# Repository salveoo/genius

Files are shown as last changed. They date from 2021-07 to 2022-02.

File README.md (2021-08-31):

# Artillery Genius to Switchwire
This is my journey in converting an Artillery Genius to Switchwire. \
_discord salveo#6988 if you have any question_

<p align="center">
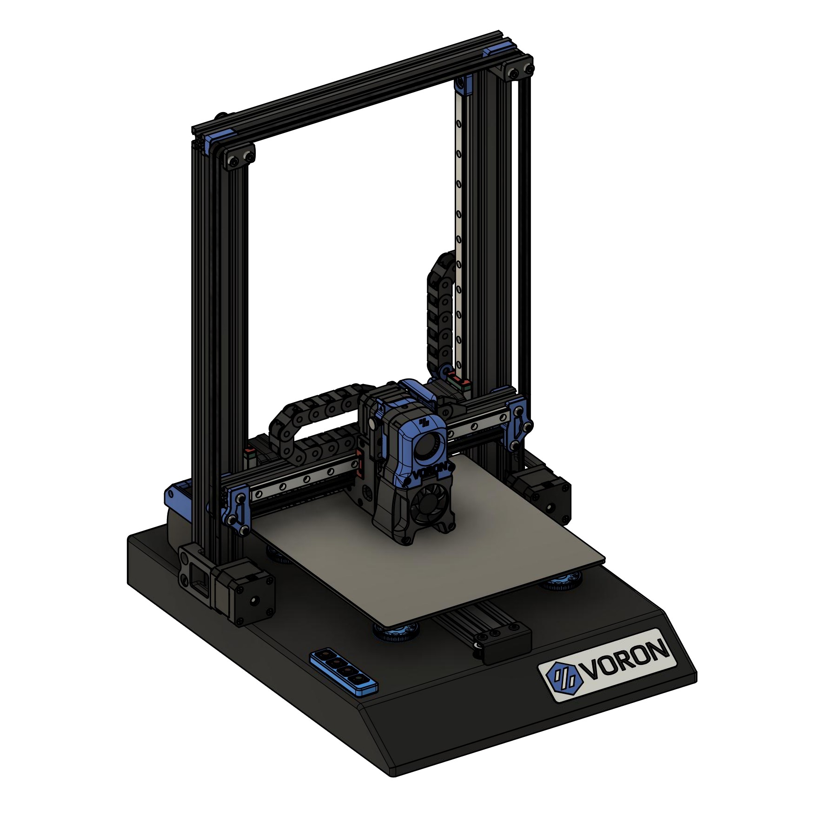
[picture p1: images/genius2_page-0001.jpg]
  
</p>

## SW 193 ♥

<p align="center">
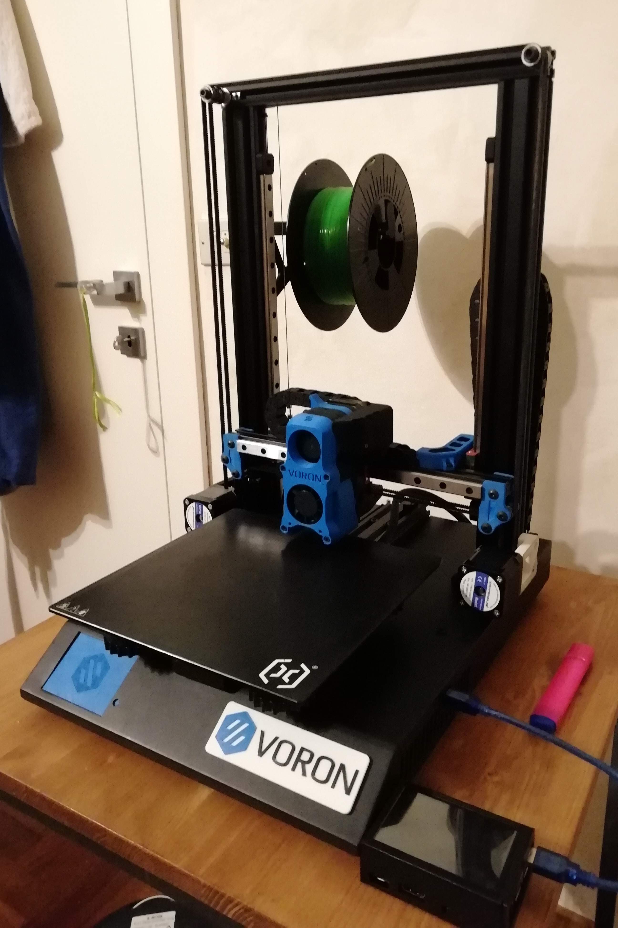
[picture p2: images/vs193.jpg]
  
</p>

## This conversion is based on [Gizzle’s Ender 3 conversion](https://github.com/VoronDesign/VoronUsers/tree/master/printer_mods/Gizzle/ender-3_(pro)_switchwire "Title")

I reused the following parts:
* motor mounts
* upper blocks assembly
* Z bearing blocks
* keybak mount

## Build information
This mod will shorten the X travel by 10mm because of the narrow vertical extrusions but you will gain 20mm of travel in Z. \
**The build volume is 220x230x270** \

## Build overview
_Front and Left_
<p align="center">
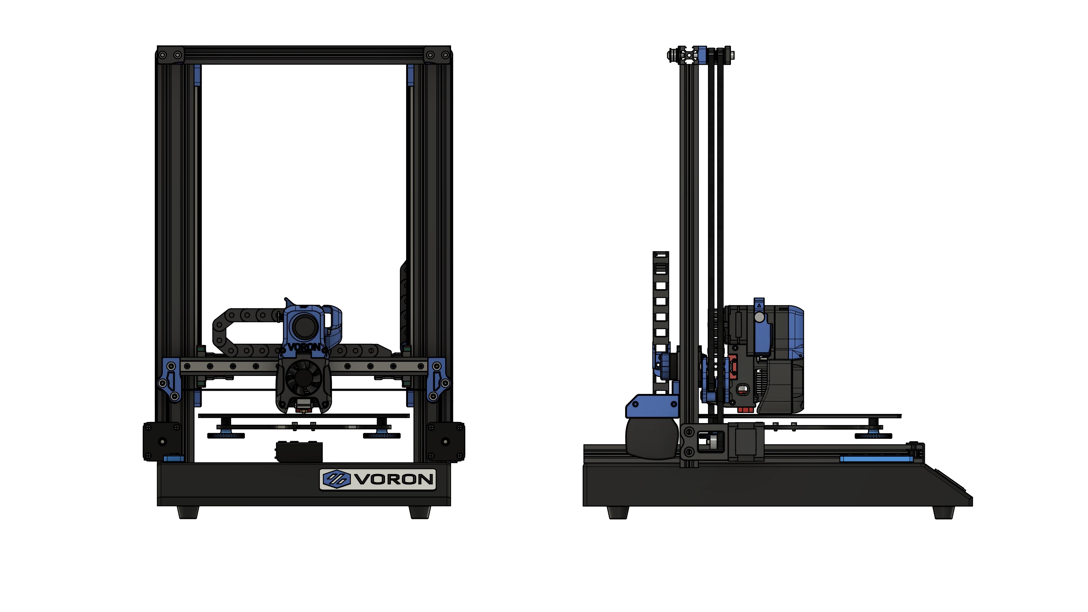
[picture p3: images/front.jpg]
  
</p>

_Back and Right_
<p align="center">
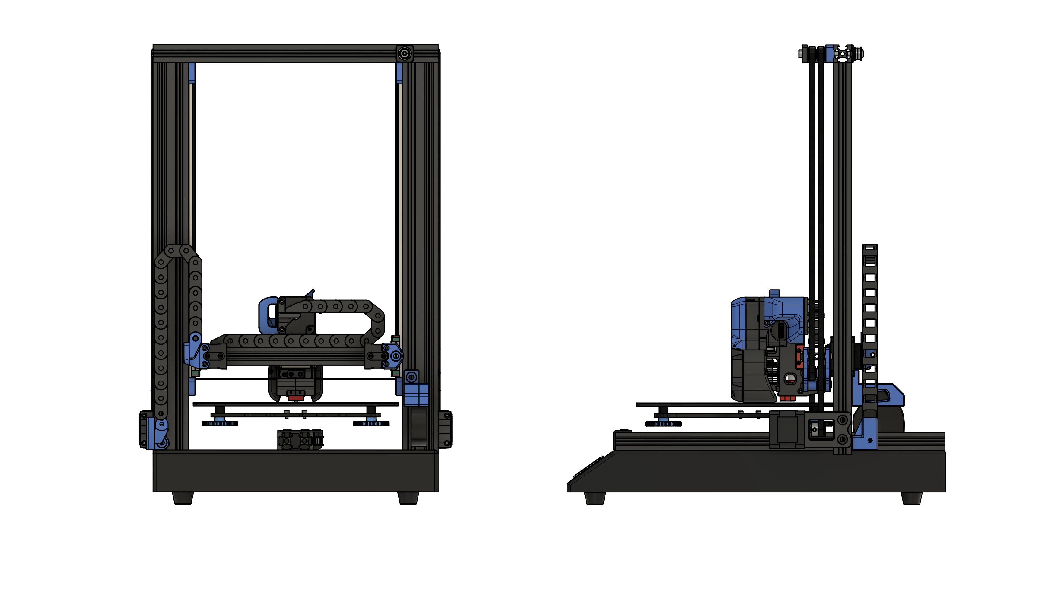
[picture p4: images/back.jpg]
  
</p>

## Reuse parts
You can reuse a good amount of parts from the Genius:
* MCU (Mks gen L)
* PSU
* Y assembly
* All the stepper motors except the extruder one
* 4020 blower
* 4010 fan
* 2040 vertical extrusions \
**At the moment, the TFT screen is not compatible with Klipper, you won’t be able to use it.**

## BOM
[See the Switchwire BOM for links to products](https://vorondesign.com/sourcing_guide?model=VS)

### Frame
* 2020 extrusion 320mm – 1pcs (top extrusion)
* 2020 extrusion 310mm – 1pcs (x axis extrusion)
### Motion
* MGN12H linear rail 330mm – 2pcs (z axis)
* MGN12H linear rail 270mm – 1pcs (x axis)
* GT2 belt – 5 meters
* GT2 20t pulley – 3 pcs
* F695 Bearing – 20 pcs
### Electronics
* Raspberry for running klipper
* SPDT KW10 Limit Micro Switch (for x-axis)
* Omron TL-Q5MC2 - NPN Inductive Probe (if you want bed mesh leveling,I reused the stock endstop for z)
* 20mm NEMA17 for the extruder (NEMA17 Motor 17HS08-1004S)
### Misc
* Loctite Blue Threadlocker (or nail polish)
* Key-Bak (you can use this cheaper alternative (https://it.aliexpress.com/item/1005001273995297.html)

### Cable Management	
* 24 AWG PTFE
* 20 AWG PTFE
* 10x11 Cable Chain
* connectors

### Fasteners
_Make sure you order spare fasteners in case I miscounted them_

<p align="center">
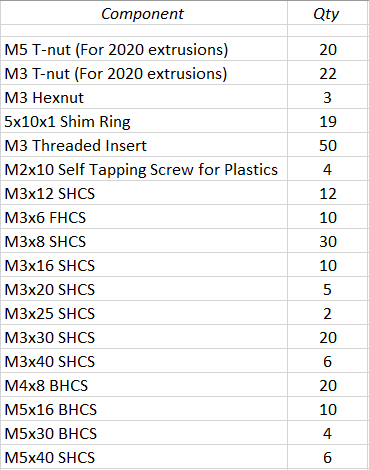
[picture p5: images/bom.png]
  
</p>

### Extra
* hardware for the Afterburner (check sw bom)

## GCODE buttons mod
To cover the unused usb port I created a keyboard of 4 buttons that call a gcode macro. \
Buttons used: 12x12x4.3 => [aliexpress](https://it.aliexpress.com/item/32807507828.html)

<p align="center">
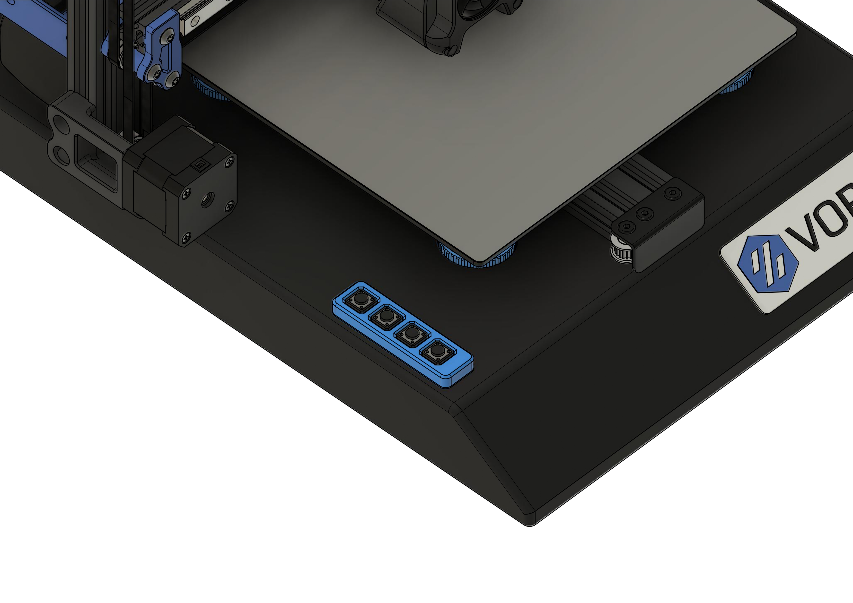
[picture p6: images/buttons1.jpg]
  
</p>

Solder one side of the button to a data pin, the other goes to GND. \
Then close the lid and route the cables through the usb hole.
<p align="center">
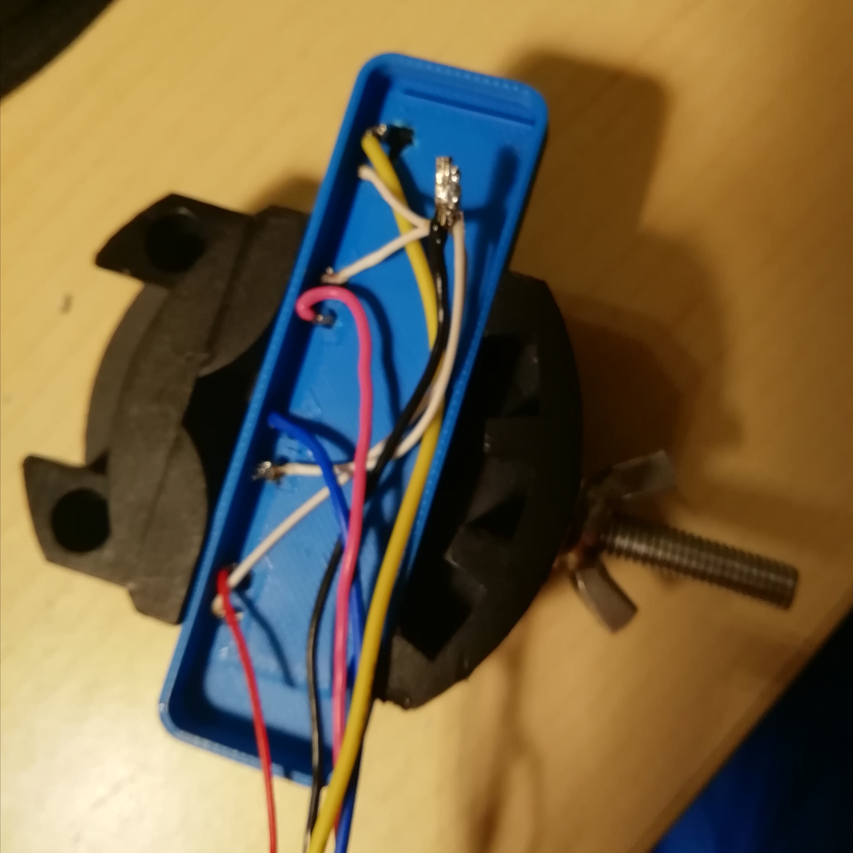
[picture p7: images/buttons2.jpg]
  
</p>

Product in action
<p align="center">
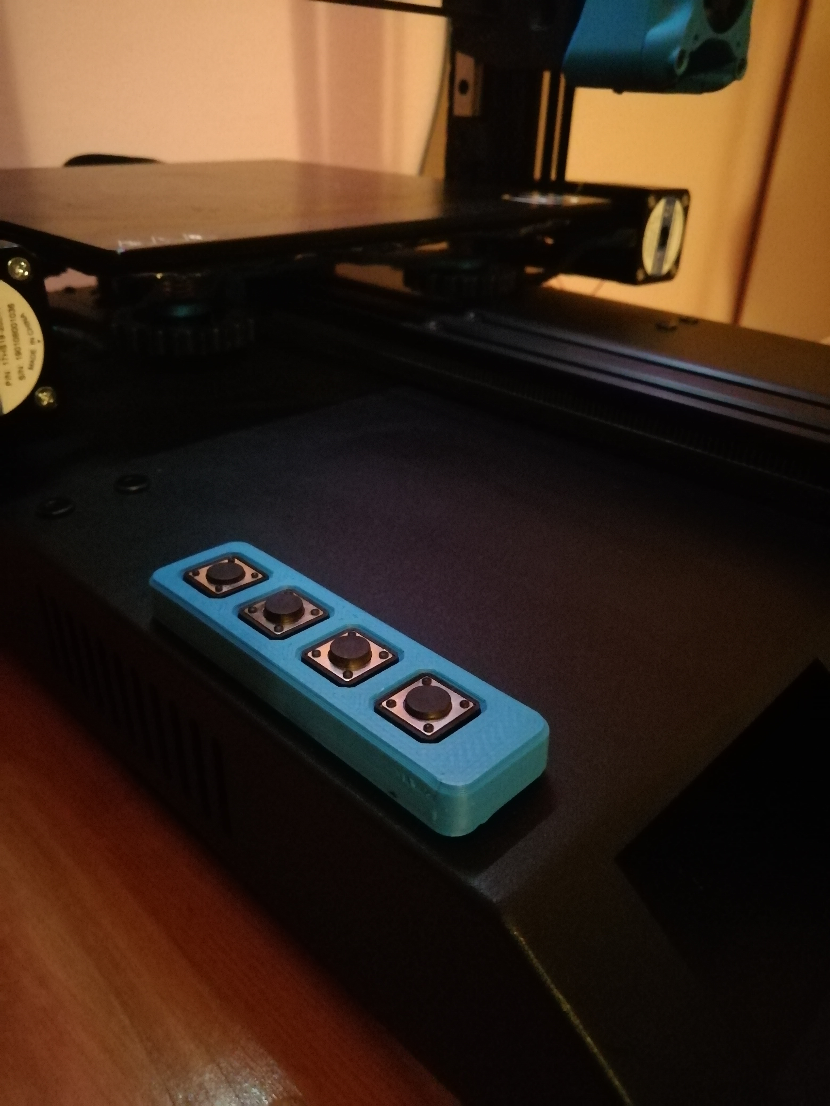
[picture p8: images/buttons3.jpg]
  
</p>

## Full metal idlers
If you want your top idlers to be sturdier you can reuse the old pulley to act as an m5 spacer.
<p align="center">
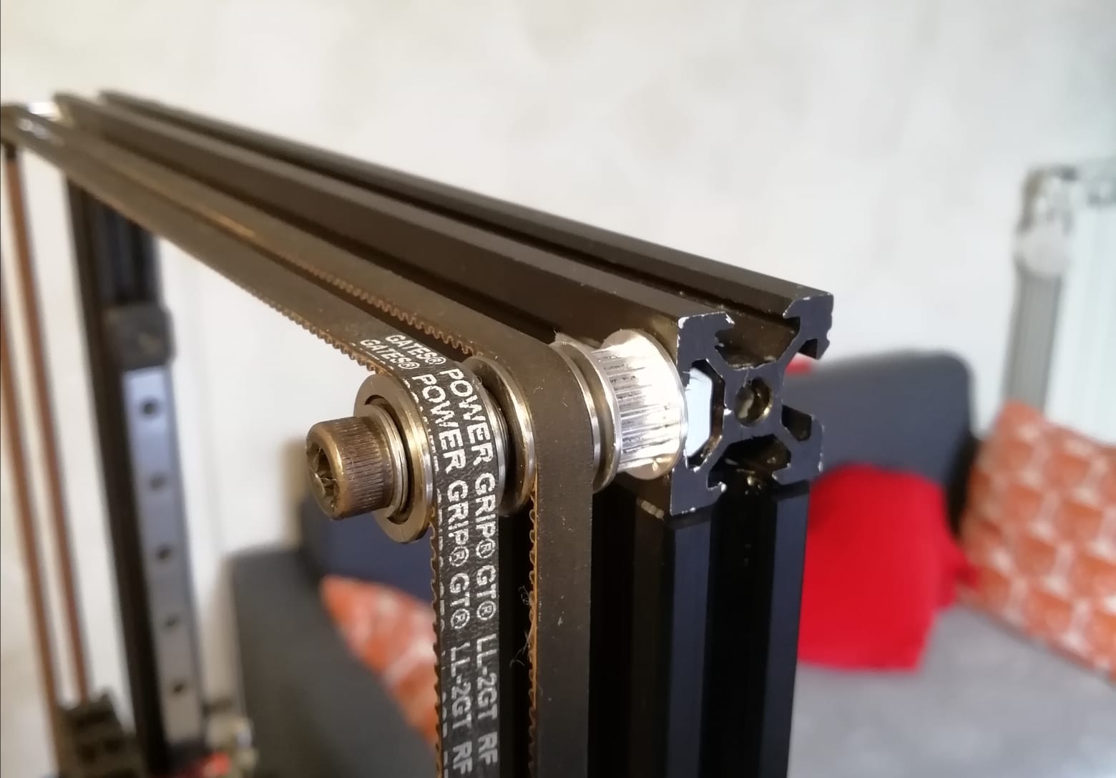
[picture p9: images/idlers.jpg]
  
</p>

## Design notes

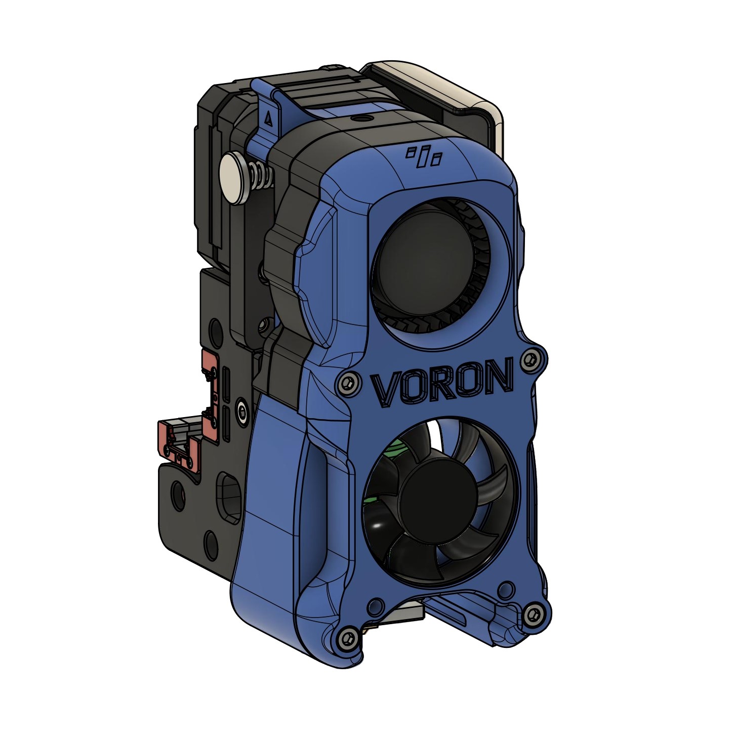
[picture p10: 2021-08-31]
images/mod1.jpg

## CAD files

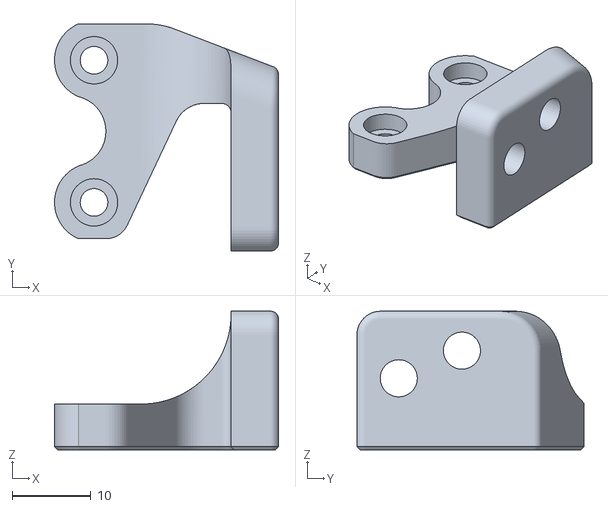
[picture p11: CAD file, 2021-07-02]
STL/CABLE_CHAINS/Z_chain_mount.stl
28.4 x 28.8 x 17.6

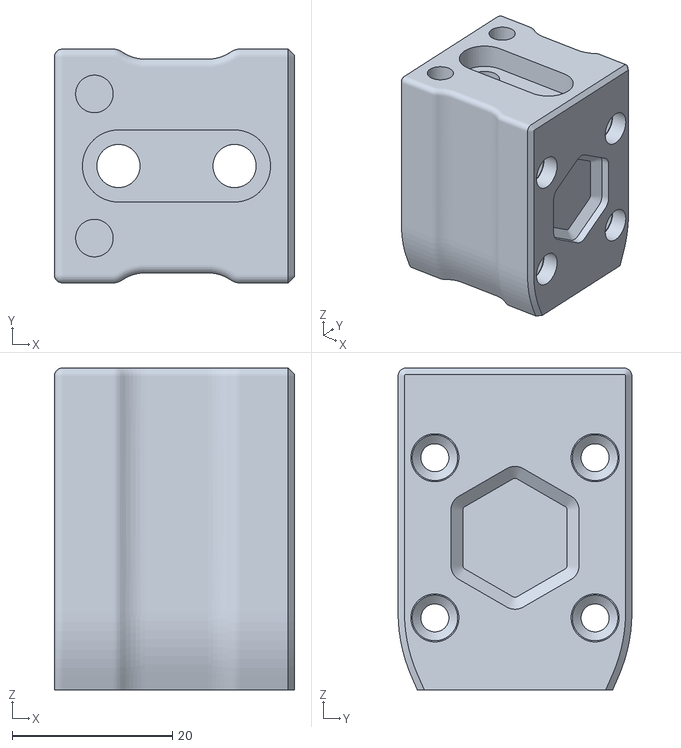
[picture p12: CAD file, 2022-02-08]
STL/GANTRY/Z-Bearing_Block_Right_x1.stl
30.0 x 29.2 x 40.2

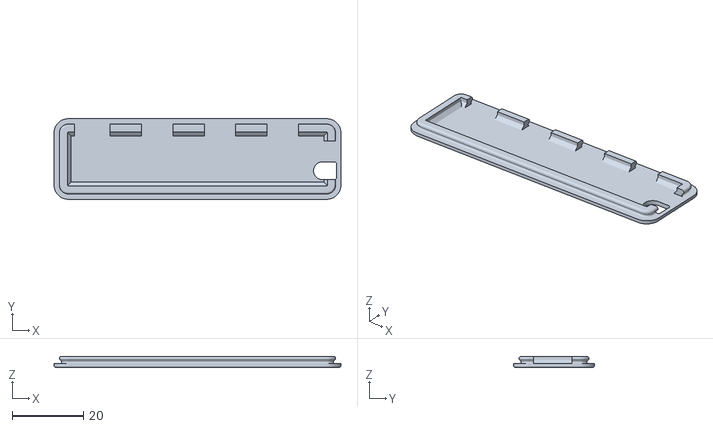
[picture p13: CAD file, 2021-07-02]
STL/GCODE_BUTTONS_MOD/bottom.stl
80.4 x 22.6 x 3.20

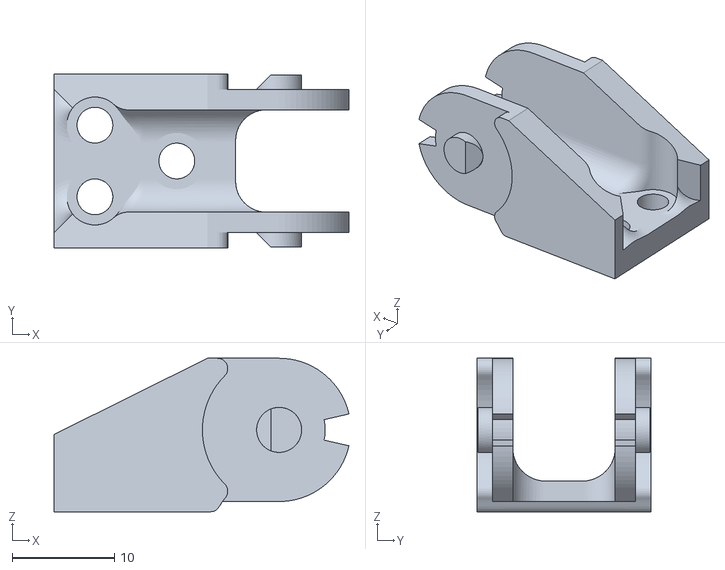
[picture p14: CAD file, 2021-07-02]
STL/CABLE_CHAINS/china_chain_endlink_male.stl
28.8 x 17.0 x 15.0

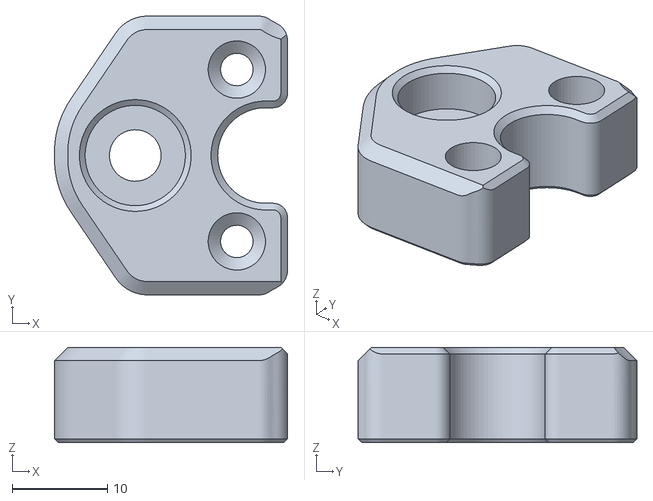
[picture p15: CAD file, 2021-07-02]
STL/GANTRY/keybak_gantry_anchor(ALIEXPRESS keyback).stl
24.4 x 29.2 x 10.0

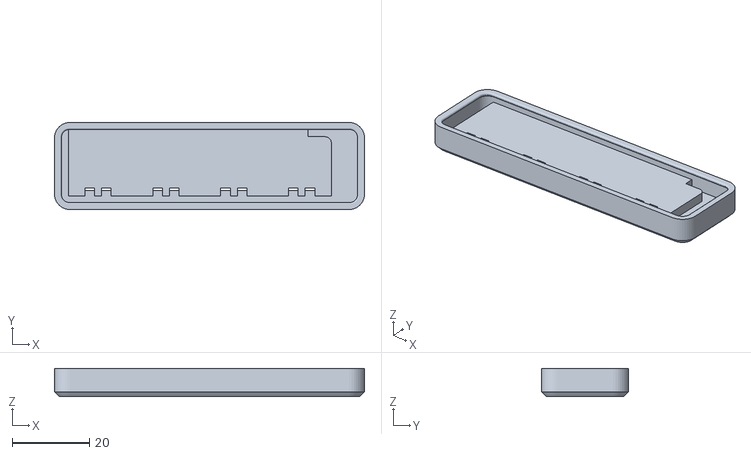
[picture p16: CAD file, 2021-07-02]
STL/GCODE_BUTTONS_MOD/top.stl
80.4 x 22.6 x 7.28

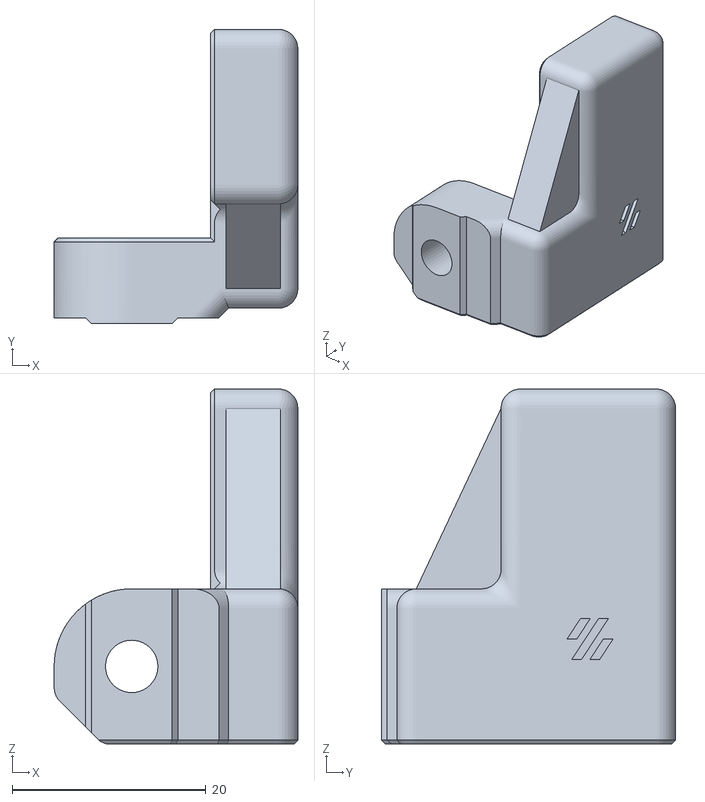
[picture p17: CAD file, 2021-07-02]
STL/CABLE_CHAINS/Z_chain_lower_mount.stl
25.1 x 30.3 x 36.6

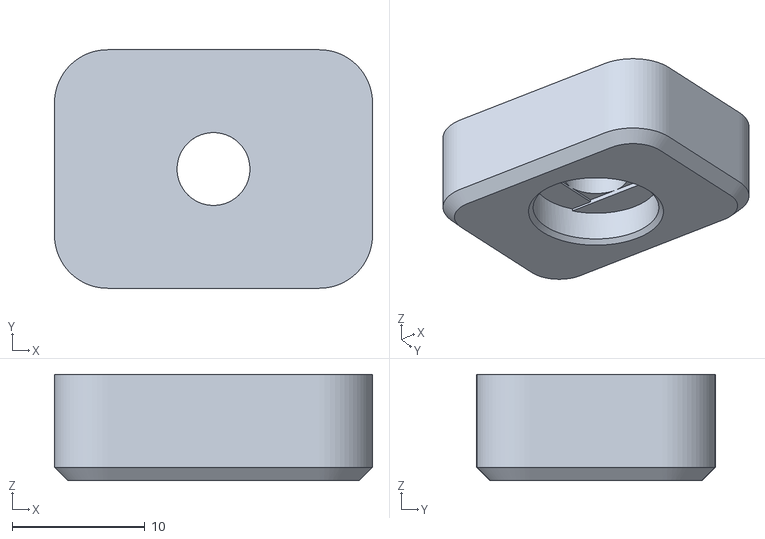
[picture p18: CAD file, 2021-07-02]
STL/GANTRY/z_carriage_stop_top X2.stl
24.0 x 18.0 x 8.00

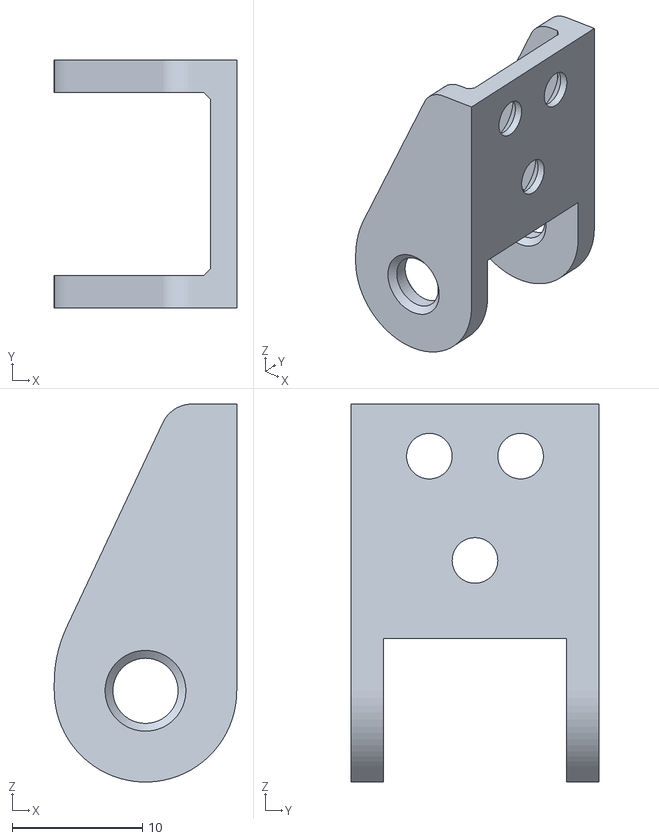
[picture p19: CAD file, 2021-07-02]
STL/CABLE_CHAINS/china_chain_endlink_female.stl
14.0 x 19.0 x 29.0

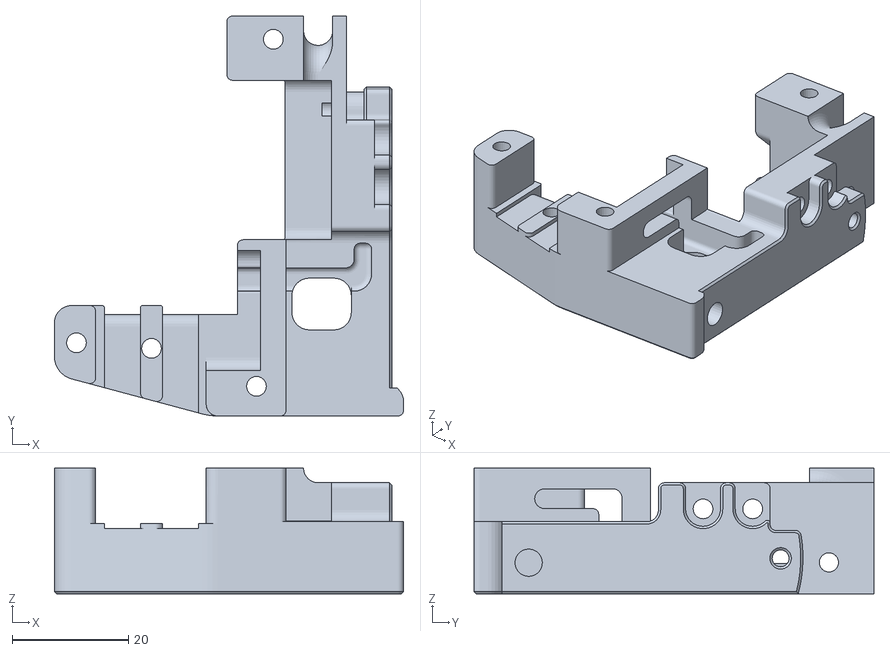
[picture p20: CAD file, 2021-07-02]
STL/GANTRY/x_carriage_frame_right_x1.stl
60.0 x 68.8 x 21.6

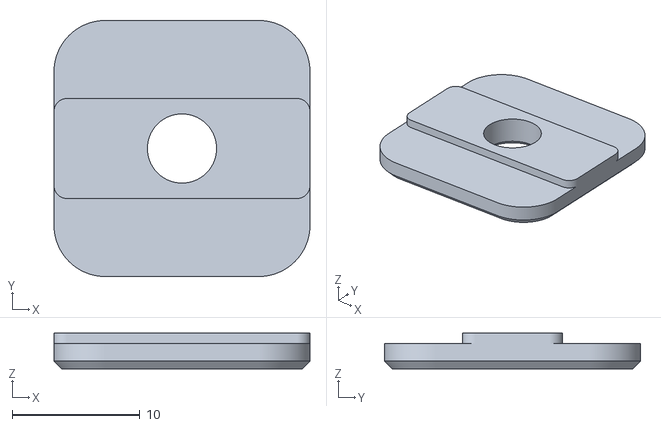
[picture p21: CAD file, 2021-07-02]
STL/GANTRY/Keyback-Idler_x1.stl
20.0 x 20.0 x 2.80

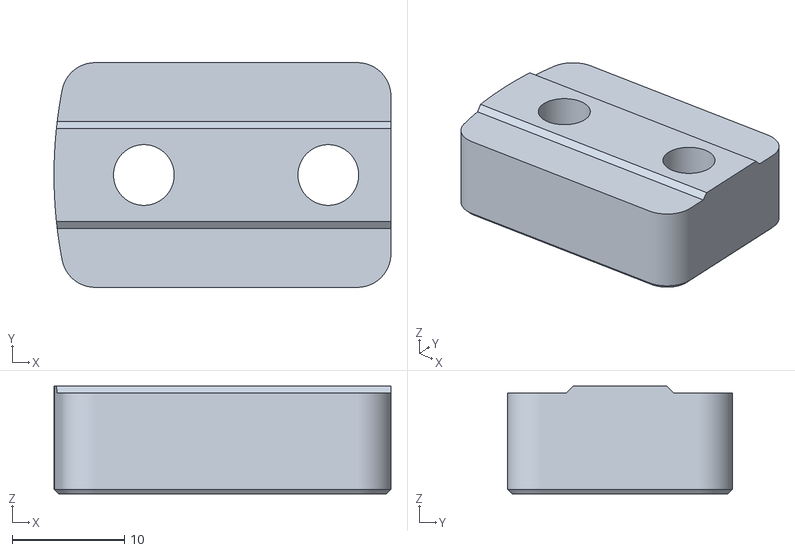
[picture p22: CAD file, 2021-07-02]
STL/GANTRY/[a]_Upper-Block_Left_Base_x1.stl
30.0 x 20.0 x 9.60

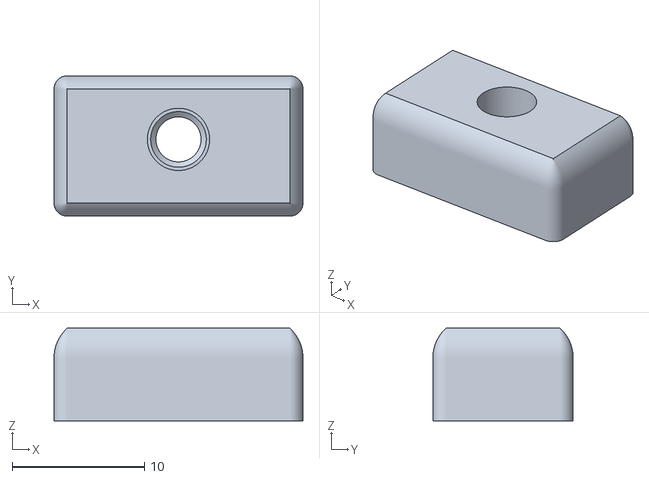
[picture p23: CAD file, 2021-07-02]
STL/GANTRY/[a]_Belt-Clip_x2.stl
18.8 x 10.6 x 7.00

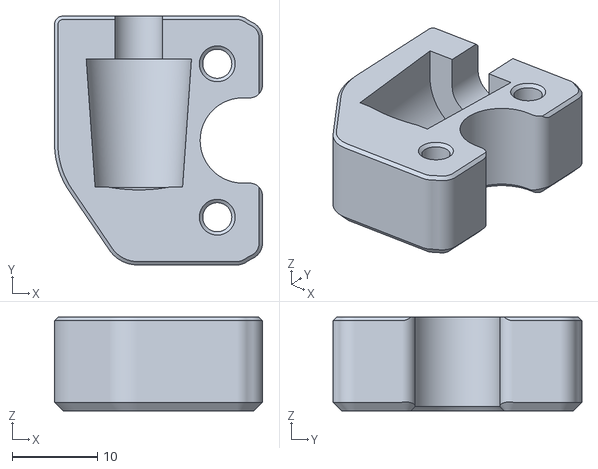
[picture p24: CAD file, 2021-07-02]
STL/GANTRY/keybak_gantry_anchor (original keybak).stl
24.4 x 29.2 x 11.0

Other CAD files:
STL/GANTRY/Z-Bearing_Block_Left_Keybak_x1.stl
STL/GANTRY/Keyback-Mount (ALIEXPRESS keybak).stl
STL/GANTRY/x_carriage_frame_left_x1.stl
STL/GANTRY/[a]_Upper-Block_Right_Base_x1.stl
STL/GANTRY/Keyback-Mount_Back_x1 (original keybak).stl
STL/GANTRY/Keyback-Mount_Front_x1 (original keybak).stl
STL/GANTRY/z_carriage_stop_bottom X2.stl

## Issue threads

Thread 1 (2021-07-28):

KeyBak Mount Front Vertical

edelapena-dev, 2021-07-28:
Thank you for sharing this MOD, I am making the same change but on a SWX1, the original Keybak front mount does not work because there is no space between the bed and the aluminum frame, in your photos you can see that you modified it to put it Vertical , but it is not in the STL folder, please can you share that piece.

Thanks again.

salveoo, 2021-07-28:
Hi, I am happy you enjoyed the mod. I am currently on holiday so until
monday I can't access my computer. I am going to send you the step file
when I reach home. If you want to contact me on discord salveo#6988.

Google day

Il mer 28 lug 2021, 17:54 edelapena-dev ***@***.***> ha
scritto:

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

edelapena-dev, 2021-07-28:
Thanks ! , enjoy your vacation .

Closed 2021-07-28.

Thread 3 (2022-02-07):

2 copies of Z-Bearing_Block_Left_Keybak_x1.stl needed

gonchogsm, 2022-02-07:
Great work! I'm preparing the STL to print and I think you need 2 copies of [Z-Bearing_Block_Left_Keybak_x1.stl](https://github.com/salveoo/genius/blob/main/STL/GANTRY/Z-Bearing_Block_Left_Keybak_x1.stl) instead of 1 as the name says.

salveoo, 2022-02-08:
Thanks! I forgot to add Z-Bearing_Block_Right_x1. Now it's here https://github.com/salveoo/genius/blob/main/STL/GANTRY/Z-Bearing_Block_Right_x1.stl. Enjoy your build :)

gonchogsm, 2022-02-08:
Thanks!

Closed 2022-02-09.

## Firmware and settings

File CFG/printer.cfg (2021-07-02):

# my cfg, RPI 3B+ and MKS GEN L

[include mainsail.cfg]

[mcu]
serial:dev/serial/by-id/usb-1a86_USB_Serial-if00-port0 
pin_map: arduino
restart_method: command

[printer]
kinematics: corexz
max_velocity: 300
max_accel: 4000
max_z_velocity: 300
max_z_accel: 1000

[bed_screws]
screw1: 40,40
screw2: 190,40
screw3: 190,190
screw4: 40,190

[virtual_sdcard]
path: /home/pi/gcode_files

[stepper_x]
step_pin: ar54
dir_pin: !ar55
enable_pin: !ar38
step_distance: .0125
endstop_pin: ^ar3
position_min: -2
position_endstop: 220
position_max: 220
homing_speed: 80

[stepper_z]
step_pin: ar46
dir_pin: !ar48
enable_pin: !ar62
step_distance: .0125
endstop_pin: ^ar18
position_endstop: 0
position_max: 250
homing_speed: 80
homing_retract_dist: 3.0
homing_retract_speed: 80
second_homing_speed: 5.0

[stepper_y]
step_pin: ar60
dir_pin: ar61
enable_pin: !ar56
step_distance: .0125
endstop_pin: !ar14
position_min: 0
position_endstop: 0
position_max: 230
homing_speed: 80

[homing_override]
set_position_z: 0
gcode:
  G90
  SET_GCODE_OFFSET Z=-0.16
  G1 Z2 F300
  G28 X0 Y0
  G28 Z
  G1 Z5 F300  

#############################Heaters & Extruder####################################

[extruder]
step_pin: ar26
dir_pin: !ar28
enable_pin: !ar24
step_distance: 0.0024
nozzle_diameter: 0.400
filament_diameter: 1.750
heater_pin: ar10
sensor_type: EPCOS 100K B57560G104F
sensor_pin: analog13
pressure_advance = 0.05
control: pid
pid_Kp: 18.877
pid_Ki: 1.040
pid_Kd: 85.656
min_temp: 0
max_temp: 275
#max_extrude_cross_section:
#instantaneous_corner_velocity: 1.000
max_extrude_only_distance: 100.0
#max_extrude_only_velocity:
#max_extrude_only_accel:
#pressure_advance: 0.0
#pressure_advance_smooth_time: 0.040

#Hotend Fan
[heater_fan my_nozzle_fan]
pin: ar7
heater: extruder
heater_temp: 50.0
fan_speed: 1.0

#PartCooling
[fan]
pin: ar9

[heater_bed]
heater_pin: ar8
sensor_type: EPCOS 100K B57560G104F
sensor_pin: analog14
control: pid
pid_Kp: 43.155
pid_Ki: 0.668
pid_Kd: 697.499
min_temp: 0
max_temp: 130

############################## MACROS ######################################

[gcode_macro PARK_MACRO]
default_parameter_X: 0
default_parameter_Y: 0
default_parameter_Z: 30
gcode:
	M117 PARKING..
	G91
	G1 E-3.0 F1500
	G1 Z{Z}
	G90
	G1 X{X} Y{Y} F3000
	
[gcode_macro UNLOAD]
gcode:
	G91
	G1 E5.0 F1200
	G1 E-50.0 F2000
	G1 E-50.0 F5000
	G90
        
[gcode_macro M600]
gcode:
	PAUSE_MACRO
	UNLOAD

[gcode_macro PAUSE_MACRO]
gcode:
	PAUSE
	PARK_MACRO
	
[gcode_macro PURGE]
gcode:
	M117 PURGING..
	G91
	G1 E45.0 F250
	G90
        
[gcode_macro LOAD_FILAMENT]
gcode:
	M117  LOADING...
	G91
	G1 E25.0 F1000
	G1 E50.0 F2000
	G4 P900
	G1 E20.0 F250
	G90

[gcode_macro RESUME_MACRO]
gcode:
	M117  RESUMING...
	RESUME

[gcode_macro START_PRINT]
gcode:
    # Reset the G-Code Z offset (adjust Z offset if needed)
    SET_GCODE_OFFSET Z=0.0
	
[gcode_macro END_PRINT]
gcode:
    # Turn off bed, extruder, and fan
    M140 S0
    M104 S0
    M106 S0
    # Move nozzle away from print while retracting
    G91
    G1 X0 Y230 E-3 F300
    # Raise nozzle by 10mm
    G1 Z10 F3000
    G90
    # Disable steppers
    M84

[gcode_macro LEDRED]
gcode:  
	SET_PIN PIN=LED_pin_red VALUE=1

[gcode_macro LEDGREEN]
gcode:  
	SET_PIN PIN=LED_pin_green VALUE=1

[gcode_macro LEDBLUE]
gcode:  
	SET_PIN PIN=LED_pin_blue VALUE=1

[gcode_macro LEDWHITE]
gcode:  
	SET_PIN PIN=LED_pin_red VALUE=1
	SET_PIN PIN=LED_pin_green VALUE=1
	SET_PIN PIN=LED_pin_blue VALUE=1
	
[gcode_macro LEDOFF]
gcode:
	SET_PIN PIN=LED_pin_red VALUE=0
	SET_PIN PIN=LED_pin_green VALUE=0
	SET_PIN PIN=LED_pin_blue VALUE=0
	
[output_pin gantry_led]
pin: ar53
value: 1

[gcode_macro TOGGLE]
gcode:
    {% if printer["output_pin gantry_led"].value == 1.0 %}
        lights_off
    {% else %}
        lights_on
    {% endif %}

[gcode_macro lights_off]
gcode:
    SET_PIN PIN=gantry_led VALUE=0

[gcode_macro lights_on]
gcode:
    SET_PIN PIN=gantry_led VALUE=1

[gcode_macro CUSTOM_HOME]
gcode:
	G28
	G91
	G1 Z+35 F4500
	G90


############################## G-CODE BUTTONS ######################################

[gcode_button top_button]
pin: ^!ar4
press_gcode: M18

[gcode_button mid-top_button]
pin: ^!ar5
press_gcode: PURGE

[gcode_button mid-bottom_button]
pin: ^!ar6
press_gcode: CUSTOM_HOME

[gcode_button bottom_button]
pin: ^!ar11
press_gcode: TOGGLE


###################################Display#########################################
# Common EXP1 / EXP2 (display) pins
[board_pins]
aliases:
    # Common EXP1 header found on many "all-in-one" ramps clones
    EXP1_1=ar37, EXP1_3=ar17, EXP1_5=ar23, EXP1_7=ar27, EXP1_9=<GND>,
    EXP1_2=ar35, EXP1_4=ar16, EXP1_6=ar25, EXP1_8=ar29, EXP1_10=<5V>,
    # EXP2 header
    EXP2_1=ar50, EXP2_3=ar31, EXP2_5=ar33, EXP2_7=ar49, EXP2_9=<GND>,
    EXP2_2=ar52, EXP2_4=ar53, EXP2_6=ar51, EXP2_8=ar41, EXP2_10=<RST>
    # Pins EXP2_1, EXP2_6, EXP2_2 are also MISO, MOSI, SCK of bus "spi"
    # Note, some boards wire: EXP2_8=<RST>, EXP2_10=ar41
	
[filament_switch_sensor my_sensor]
pause_on_runout: True
runout_gcode:
	M600
#insert_gcode:
#   A list of G-Code commands to execute after a filament insert is
#   detected. See docs/Command_Templates.md for G-Code format. The
#   default is not to run any G-Code commands, which disables insert
#   detection.
#event_delay: 3.0
#   The minimum amount of time in seconds to delay between events.
#   Events triggered during this time period will be silently
#   ignored. The default is 3 seconds.
pause_delay: 0.5
#   The amount of time to delay, in seconds, between the pause command
#   dispatch and execution of the runout_gcode. It may be useful to
#   increase this delay if Octoprint exhibits strange pause behavior.
#   Default is 0.5 seconds.
switch_pin: ar2

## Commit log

2021-07-02 added cad
    [genius.f3d]
2021-07-02 printer.cfg upload
    [printer.cfg]
2022-02-08 added missing STL
    [Z-Bearing_Block_Right_x1.stl]
